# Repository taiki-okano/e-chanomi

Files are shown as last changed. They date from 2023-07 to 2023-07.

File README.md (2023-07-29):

# eChanomi - a self-balancing plate

The self-balancing plate from [the CPS course](https://campus.tum.de/tumonline/ee/ui/ca2/app/desktop/#/pl/ui/$ctx/WBMODHB.wbShowMHBReadOnly?$ctx=design=ca2;header=max;lang=en&pKnotenNr=3038801&pOrgNr=1) at TUM.
Chanomi comes from "茶飲み" in Japanese, which means "drinking tea".
The objective was to make a self-balancing plate with a teacup on it to carry it without spilling.
However, I would say the balancing functionality itself is not that quick from the problems.
There is a lot of space to improve this project, but I leave the work as of now here.

The original inspiration comes from the old Japanese mechanical doll called ["茶運び人形" (Chahakobi-Ningyo)](https://ja.wikipedia.org/wiki/%E8%8C%B6%E9%81%8B%E3%81%B3%E4%BA%BA%E5%BD%A2).

## Work



ezgif-3-f31c350fd3-min

## How It works

```mermaid
graph LR;
  acel(MPU6050 Accelerometer)-->comp_filter(Complementary Filter);
  gyro(MPU6050 Gyrometer)-->comp_filter;
  comp_filter-->pid(PID Controller);
  pid-->angle_calc(Calculate Output)
  angle_calc-->servo1(Servomotor 1)
  angle_calc-->servo2(Servomotor 2)
  angle_calc-->servo3(Servomotor 3)
  angle_calc-->servo4(Servomotor 4)
```

## Materials

- Raspberry Pi 3B
- MPU6050 (Accelerometer and Gyrometer)
- [Servomotors x 4](https://amzn.eu/d/0OTdLRw) - Better to use something more accurate
- [16-Channel PWM Hat](https://amzn.eu/d/6rtuQci)
- [Universal Joint](https://amzn.eu/d/5azXKrS)
- 3D Printer

## Problems

### Servomotors are not accurate enough
This makes it difficult to stabilise the plate at the zero position.
As a result, the parameters of PID are set to very low so that it does not oscillate.

### The parts are not solid enough
Since every part is made by the 3D printer, those are not solid enough for some parts.
Especially the connection between the servomotor and the arms is not solid, and it makes a lot of errors.

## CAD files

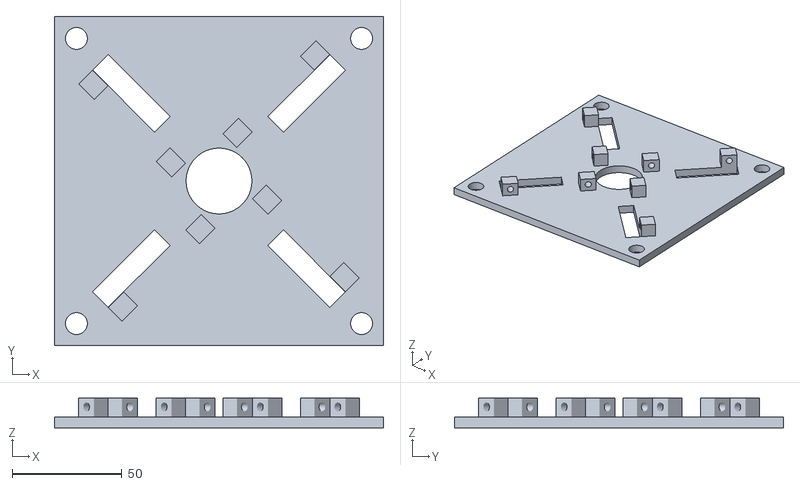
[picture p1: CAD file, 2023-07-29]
3D_models/platform_middle v3.stl
150.0 x 150.0 x 13.5

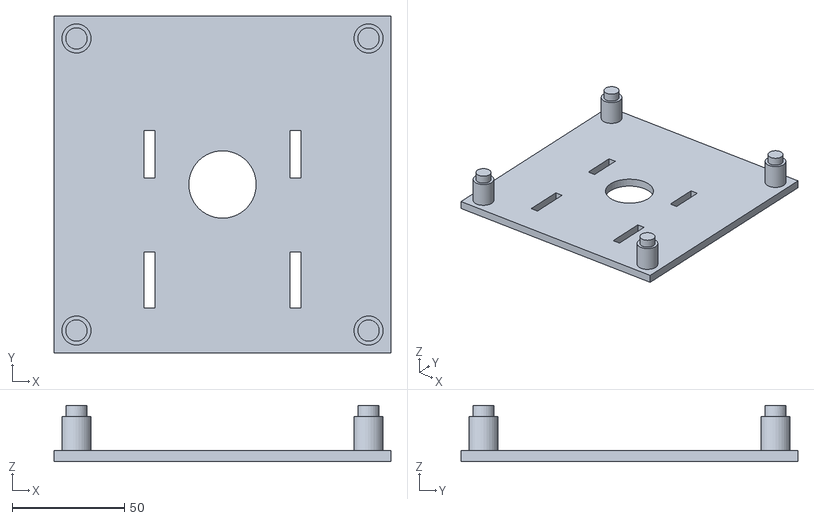
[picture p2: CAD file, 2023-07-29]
3D_models/platform_bottom v5.stl
150.0 x 150.0 x 25.0

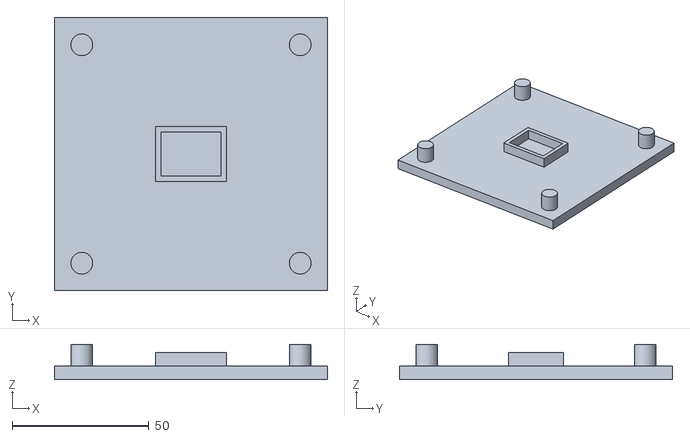
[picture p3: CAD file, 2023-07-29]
3D_models/platform_top v1.stl
100.0 x 100.0 x 13.0

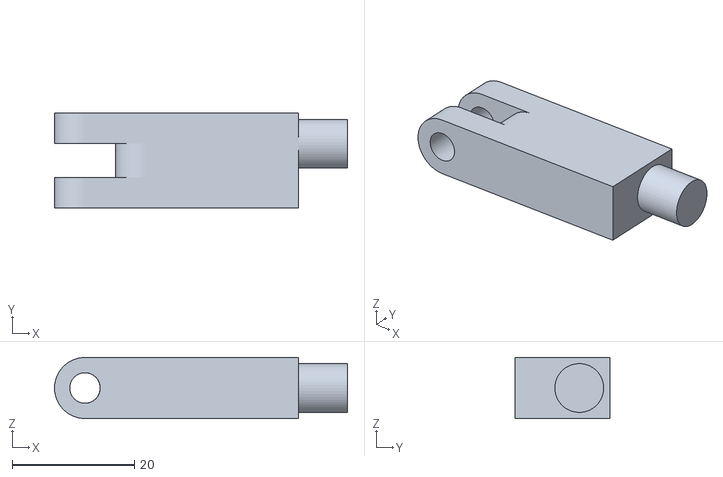
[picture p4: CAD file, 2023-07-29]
3D_models/upper_arm v3.stl
48.0 x 15.5 x 10.0

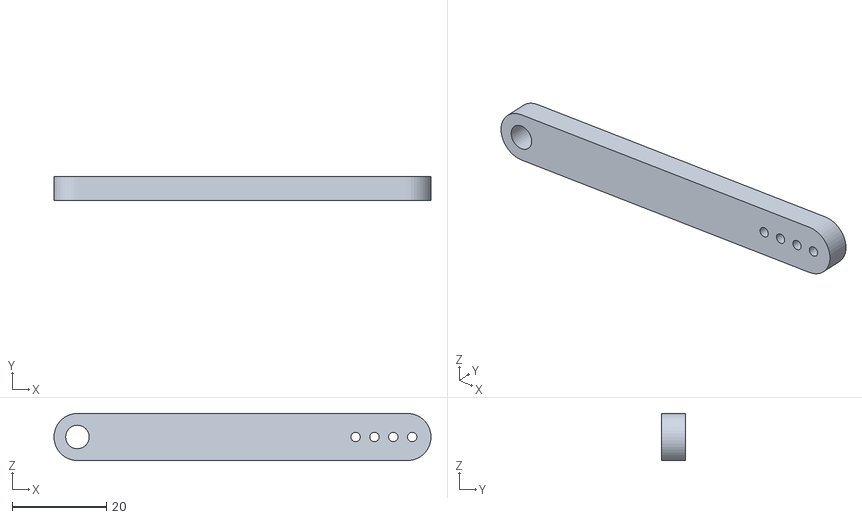
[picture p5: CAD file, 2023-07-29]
3D_models/bottom_arm v1.stl
80.0 x 5.00 x 10.0

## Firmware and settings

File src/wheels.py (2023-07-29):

import time
import RPi.GPIO as GPIO


Motor_A_EN = 4
Motor_B_EN = 17

Motor_A_Pin1 = 26
Motor_A_Pin2 = 21
Motor_B_Pin1 = 27
Motor_B_Pin2 = 18

Dir_forward = 1
Dir_backward = 0

left_forward = 1
left_backward = 0

right_forward = 0
right_backward = 1

pwn_A = 0
pwm_B = 0


def motorStop():  # Motor stops
    GPIO.output(Motor_A_Pin1, GPIO.LOW)
    GPIO.output(Motor_A_Pin2, GPIO.LOW)
    GPIO.output(Motor_B_Pin1, GPIO.LOW)
    GPIO.output(Motor_B_Pin2, GPIO.LOW)
    GPIO.output(Motor_A_EN, GPIO.LOW)
    GPIO.output(Motor_B_EN, GPIO.LOW)


def setup():  # Motor initialization
    global pwm_A, pwm_B
    GPIO.setwarnings(False)
    GPIO.setmode(GPIO.BCM)
    GPIO.setup(Motor_A_EN, GPIO.OUT)
    GPIO.setup(Motor_B_EN, GPIO.OUT)
    GPIO.setup(Motor_A_Pin1, GPIO.OUT)
    GPIO.setup(Motor_A_Pin2, GPIO.OUT)
    GPIO.setup(Motor_B_Pin1, GPIO.OUT)
    GPIO.setup(Motor_B_Pin2, GPIO.OUT)

    motorStop()
    try:
        pwm_A = GPIO.PWM(Motor_A_EN, 1000)
        pwm_B = GPIO.PWM(Motor_B_EN, 1000)
    except:
        pass


def motor_left(status, direction, speed):  # Motor 2 positive and negative rotation
    if status == 0:  # stop
        GPIO.output(Motor_B_Pin1, GPIO.LOW)
        GPIO.output(Motor_B_Pin2, GPIO.LOW)
        GPIO.output(Motor_B_EN, GPIO.LOW)
    else:
        if direction == Dir_backward:
            GPIO.output(Motor_B_Pin1, GPIO.HIGH)
            GPIO.output(Motor_B_Pin2, GPIO.LOW)
            pwm_B.start(100)
            pwm_B.ChangeDutyCycle(speed)
        elif direction == Dir_forward:
            GPIO.output(Motor_B_Pin1, GPIO.LOW)
            GPIO.output(Motor_B_Pin2, GPIO.HIGH)
            pwm_B.start(0)
            pwm_B.ChangeDutyCycle(speed)


def motor_right(status, direction, speed):  # Motor 1 positive and negative rotation
    if status == 0:  # stop
        GPIO.output(Motor_A_Pin1, GPIO.LOW)
        GPIO.output(Motor_A_Pin2, GPIO.LOW)
        GPIO.output(Motor_A_EN, GPIO.LOW)
    else:
        if direction == Dir_forward:  #
            GPIO.output(Motor_A_Pin1, GPIO.HIGH)
            GPIO.output(Motor_A_Pin2, GPIO.LOW)
            pwm_A.start(100)
            pwm_A.ChangeDutyCycle(speed)
        elif direction == Dir_backward:
            GPIO.output(Motor_A_Pin1, GPIO.LOW)
            GPIO.output(Motor_A_Pin2, GPIO.HIGH)
            pwm_A.start(0)
            pwm_A.ChangeDutyCycle(speed)
    return direction


def destroy():
    motorStop()
    GPIO.cleanup()  # Release resource


if __name__ == "__main__":
    try:
        speed_set = 70
        setup()
        motor_left(1, 1, speed_set)
        motor_right(1, 1, speed_set)
        time.sleep(1)
        motor_left(1, 0, speed_set)
        motor_right(1, 0, speed_set)
        time.sleep(1)
        motor_left(1, 1, speed_set)
        motor_right(1, 1, speed_set)
        time.sleep(1)
        motor_left(1, 0, speed_set)
        motor_right(1, 0, speed_set)
        time.sleep(1)
    except KeyboardInterrupt:
        destroy()

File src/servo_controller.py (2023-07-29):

import json
import time
import sys
from cmath import exp, log
from math import degrees, radians
from adafruit_servokit import ServoKit

kit = ServoKit(channels=16)
kit.servo[0].set_pulse_width_range(500, 2500)
kit.servo[1].set_pulse_width_range(500, 2500)
kit.servo[2].set_pulse_width_range(500, 2500)
kit.servo[3].set_pulse_width_range(500, 2500)

MIN_ANGLE = 45
MAX_ANGLE = 130

try:
    with open("error_corrections.json", "rt") as fin:
        ec = json.loads(fin.read())
except OSError:
    print("Could not read the calibration file.", file=sys.stderr)
    quit()


def set_angle_for_servomotor(channel, angle):
    """
    It is for setting the calibrated angle of a specified servomotor.

    :param channel: specifies the servomotor
    :param angle: specified the angle
    :return: nothing
    :raise ValueError: when the invalid channel or angle is given.
    """

    if not (MIN_ANGLE < angle < MAX_ANGLE and 0 <= channel <= 3):
        raise ValueError(
            f"Angle must be between {MIN_ANGLE} and {MAX_ANGLE}, but got {angle}"
        )

    kit.servo[channel].angle = angle * ec["multiply"][channel] + ec["add"][channel]


def set_angle_for_plate(theta, phi):
    """
    It sets the angles of the plate.

    :param theta: angle on the line from the servomotor 3 to 1 in radian.
    :param phi: angle on the line from the servomotor 4 to 2 in radian.
    :return: nothing
    """

    # Some magic going on here...
    def calc(theta):
        a = 8  # bottom arm
        b = 5.3  # top arm
        c = 5.7  # the distance from the center to the origin of the bottom arm rotation
        r = 5.7  # the distance from the center to the attached point on the top plate
        h = 12  # the height of the plate
        res = degrees(
            (
                -log(
                    -(
                        -c * r
                        + h * r * 1j
                        + a**2 * exp(theta * 1j)
                        - b**2 * exp(theta * 1j)
                        + c**2 * exp(theta * 1j)
                        + h**2 * exp(theta * 1j)
                        + r**2 * exp(theta * 1j)
                        + (
                            4
                            * (
                                -a * r
                                + a * c * exp(theta * 1j)
                                + a * h * exp(theta * 1j) * 1j
                            )
                            * (
                                -a * c * exp(theta * 1j)
                                + a * h * exp(theta * 1j) * 1j
                                + a * r * exp(theta * 2j)
                            )
                            + (
                                -c * r
                                + h * r * 1j
                                + a**2 * exp(theta * 1j)
                                - b**2 * exp(theta * 1j)
                                + c**2 * exp(theta * 1j)
                                + h**2 * exp(theta * 1j)
                                + r**2 * exp(theta * 1j)
                                - c * r * exp(theta * 2j)
                                - h * r * exp(theta * 2j) * 1j
                            )
                            ** 2
                        )
                        ** (1 / 2)
                        - c * r * exp(theta * 2j)
                        - h * r * exp(theta * 2j) * 1j
                    )
                    / (
                        2
                        * (
                            -a * r
                            + a * c * exp(theta * 1j)
                            + a * h * exp(theta * 1j) * 1j
                        )
                    )
                )
                * 1j
            ).real
        )

        if res > 90:
            return 180 - res

        return res

    set_angle_for_servomotor(0, calc(theta))
    set_angle_for_servomotor(1, calc(phi))
    set_angle_for_servomotor(2, calc(-theta))
    set_angle_for_servomotor(3, calc(-phi))


if __name__ == "__main__":
    set_angle_for_plate(radians(0), radians(0))

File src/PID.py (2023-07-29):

import time

class PID:
    def __init__(self, kp, ki, kd):
        """
        Set up the PID control.

        :param kp: the value for Kp
        :param ki: the value for Ki
        :param kd: the value for Kd
        """

        self.kp = kp
        self.ki = ki
        self.kd = kd
        self.err_sum = 0
        self.prev_err = 0
        self.prev_time = 0

    def generate(self, err):
        """
        Generate the output of PID.

        :param err: new err
        :return: the result of PID
        """

        if self.prev_time == 0:
            self.prev_time = time.time()
            self.err_sum += err
            self.prev_err = err
            return self.kp * err 

        cur_time = time.time()
        elapsed_time = (cur_time - self.prev_time)
        self.prev_time = cur_time

        self.err_sum += err
        res = self.kp * err + self.ki * self.err_sum * elapsed_time + self.kd * (err - self.prev_err) / elapsed_time
        self.prev_err = err

        return res
